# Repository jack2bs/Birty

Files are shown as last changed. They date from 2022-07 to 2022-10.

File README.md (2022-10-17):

# Birty the Robot

Birty is a recursive backronym for Birty Is a Robot, Thank You.

As part of my getting acquainted with robotics so as to continue in a leadership capacity in the Princeton Robotics Club, I set out to build a classic and simple, but well designed and well programmed robot which could drive in straight lines, turn accurate angles, avoid obstacles in it's path, and do it all autonomously. While these goals may not sound particularly ambitious or impressive, they are the baseline and the scaffolding for what a robot needs to be able to do.

I am proud of Birty. Birty is my most polished large project to date. The part-selection was, with one exception, well thought out. The electronics are well designed. The 3d structure of the Robot was well planned. The code is well written; it's fast, self-documenting (and documented with comments), and highly functional.

My success building Birty came on the back of the shortcomings of past projects, some of which never lived up to their potential simply due to my mistakes and inexperience. I learned from my mistakes, and I improved. I organized the project better. I worked with each sensor and electrical component before I used them to make sure they functioned as I expected them to. I tested each bit of code before moving onto another function. I took the time to do things right, and in the end it was the fastest I've ever completed a project. 

# Parts and justifications

+ Microcontroller
	+ 1 x [ATMEGA32u4](https://www.digikey.com/en/products/detail/microchip-technology/ATMEGA32U4-AUR/2238241)
	+ The Atmega32u4 is more than powerful enough for the tasks laid out, and since I had experience with it and had some in my supplies (every MCU was out of stock at the time), this was a no-brainer. An I2C bus (using the TWI peripheral) for sensor communications, USART for debugging over bluetooth, GPIO for driving motors, pin change interrupts for reading encoders, and more than enough timers for task scheduling.
+ Distance Sensors
	+ 8 x [Adafruit VL6180x](https://www.adafruit.com/product/3316)
	+ The VL6180x from STM was a good choice because it has great accuracy at low distance ranges which is extremely important for obstacle detection and avoidance for a robot of Birty's size. I chose the 6180x over other sensors in the lineup since it is the only one with a register map available, allowing me to bypass STM's poorly regarded API and simply build an I2C communication layer myself. I chose the Adafruit breakouts so that I wouldn't have to make them myself, and so that I had logic level shifting from 5v to 3.3v on both the interrupt and xshut signal lines.
+ Gyroscope
	+ 1 x [MinImu-9 v5](https://www.pololu.com/product/2738)
	+ This was perhaps the one mistake I made in part selection. The MiniImu-9 v5 from Polulu is a good IMU, but it doesn't have onboard fusion calculation and the speed of the Atmega32u4 makes a complex fusion calculation a challenge. In the future I would lean more towards something like a BNO055 from Bosch, which has on board fusion calculations and outputs roll pitch and yaw, as opposed to x, y, and z for a gyroscope, accelerometer, and magnetometer seperately.
+ Motors
	+ 2 x [Regular DC motors](https://www.adafruit.com/product/4639)
	+ 2 x [Stepper Motors](https://www.adafruit.com/product/4411)
	+ I have both stepper and DC motors and I am able to interchange them as I see fit. The choices here weren't too important but I wanted them as small as I could find, and so that is what I got. 
+ Motor mounts
	+ 1 x [DC Motor Mount](https://www.pololu.com/product/989)
	+ 2 x [Stepper Mount](https://www.pololu.com/product/3435)
+ DC Motor Driver (H Bridge)
	+ 4 x [H Bridges](https://www.adafruit.com/product/4489)
	+ I tested these H bridges on a breadboard before using them on Birty and they proved to be simple and effective.
+ Wheels
	+ 1 x (2 wheels) [Wheel pair](https://www.pololu.com/product/1424)
	+ I wanted somewhat large wheels to attempt to improve Birty's ability to handle semi-rough terrain (carpet).
+ Universal Mounting Hubs
	+ 1 x (2 hubs) [Mounting hub pair](https://www.pololu.com/product/1997)
+ Ball Casters
	+ 2 x [Ball casters](https://www.pololu.com/product/955)
	+ These were so that Birty wouldn't tilt forwards or backwards.
+ Spacers
	+ 1 x [2mm spacers](https://www.pololu.com/product/1980)
	+ 1 x [4mm spacers](https://www.pololu.com/product/1981)
	+ To space the ball casters to the right height.
+ Battery
	+ 1 x [CHAMP Portable Charger](https://www.gonimble.com/products/champ-portable-charger)
	+ I chose this battery pack because it was the smallest I could find and because I am a sucker for sustainability.
+ Battery Mounting
	+ 3 x [Battery Mounts](https://www.pololu.com/product/2677)
	+ I'll explain the battery mounting strategy further when I get to mechanical design.
+ Wire to Board conns
	+ 2 x [6 Pos Wire to Board](https://www.digikey.com/en/products/detail/on-shore-technology-inc/OSTVN06A150/1588866) and 1 x [2 Pos Wire to Board](https://www.digikey.com/en/products/detail/on-shore-technology-inc/OSTVN02A150/1588862)
+ Shift registers
	+  1 x [Shift Register](https://www.digikey.com/en/products/detail/texas-instruments/SN74HCS264DR/13562988)
	+ I'll get into the purpose of the shift register when I discuss the electronics.
+ Assorted SMD Resistors and Capacitors
	+ 3 x 5k R
	+ 2 x 10k R
	+ 1 x 100 R
	+ 2 x 22 R
	+ 6 x 0.1uF C
	+ 1 x 1uF C
	+ 2 x 22pF C
	+ Pushbuttons
	+ 16Mhz Crystal
	+ USB Receptacle
+ Header Pins
	+ 9 x [6 Pos Female Header pins](https://www.digikey.com/en/products/detail/sullins-connector-solutions/PPPC061LFBN-RC/810178)
	+ 1 x [5 Pos Female Header Pins](https://www.digikey.com/en/products/detail/sullins-connector-solutions/PPPC051LFBN-RC/810177)

# Electrical design
After choosing parts I set out to design the schematic and circuit boards. This process was relatively straight forward, except I had to find a way to use as few GPIO pins as possible. The first measure I took was introducing a shift register to access the xshut pins on the 8 VL6180x sensors. I needed to be able to shutdown the sensors one at a time so that I could change their I2C addresses away from their default of 0x29, and so a shift register allowed me to start them all shutdown, and then restart them and set their addresses one at a time. Next, I realized that each of the interrupt pins on the VL6180x sensors could be set as open drain, and thus I could attach them all to one GPIO pin and poll them to see which one triggered an interrupt. These two tricks saved me 6 and 7 GPIO pins each, such that by the end I had 4 extra GPIO pins not being used. The final schematic looked like this:
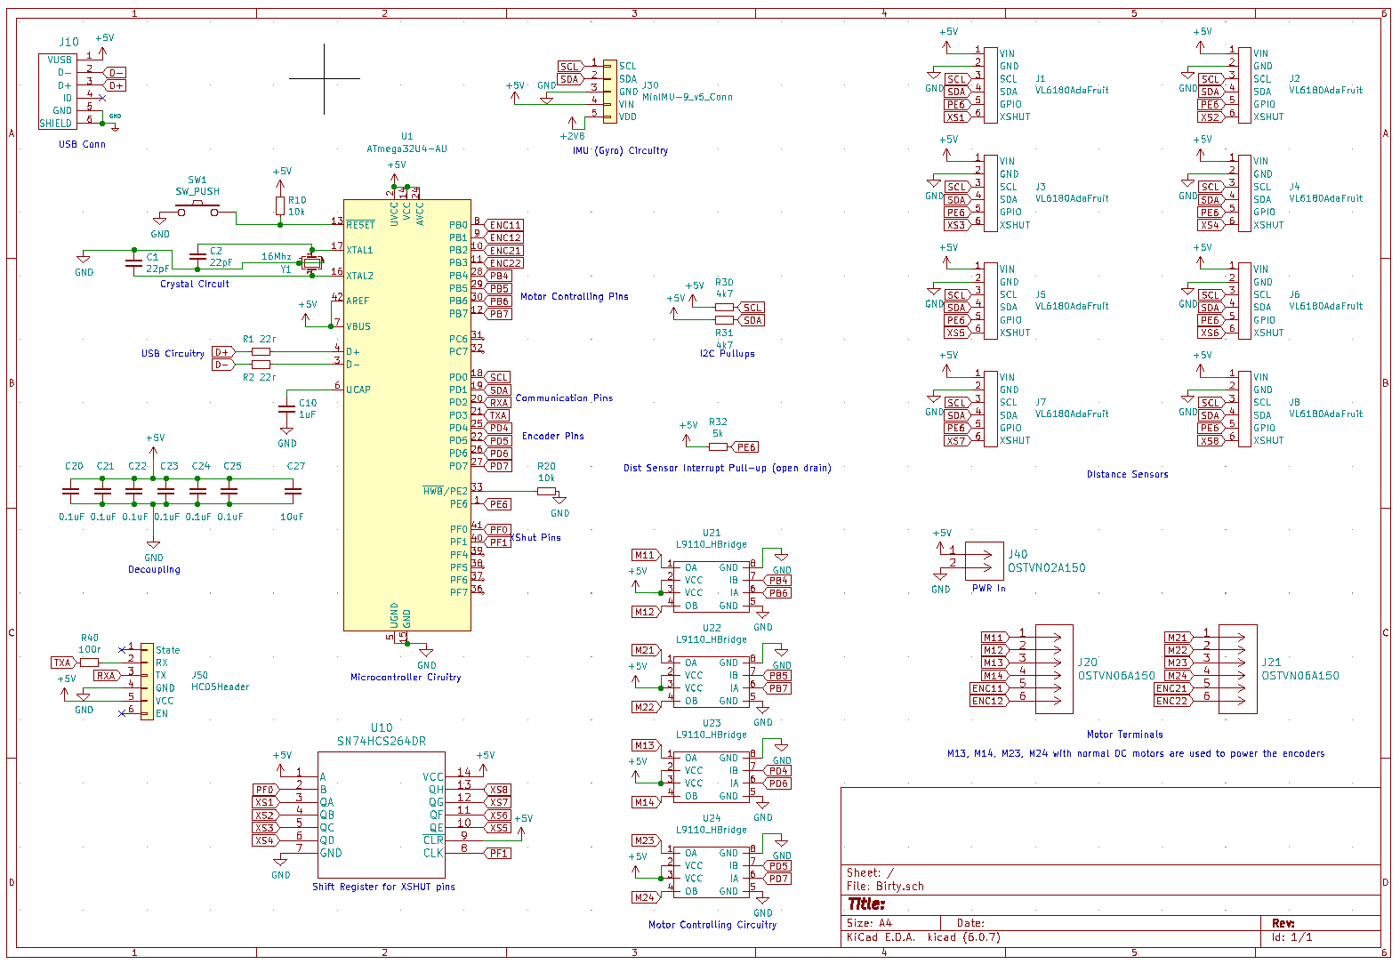
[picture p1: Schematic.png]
Schematic Image


I took this schematic and used it to produce a circuit board. I wanted every component on the top layer, which was not too difficult considering there was no real size constraint, and I wanted as large of a ground layer on the bottom layer of the board as possible, so I did the vast majority of my routing on the top layer as well. After a few hours of routing I had the following board.
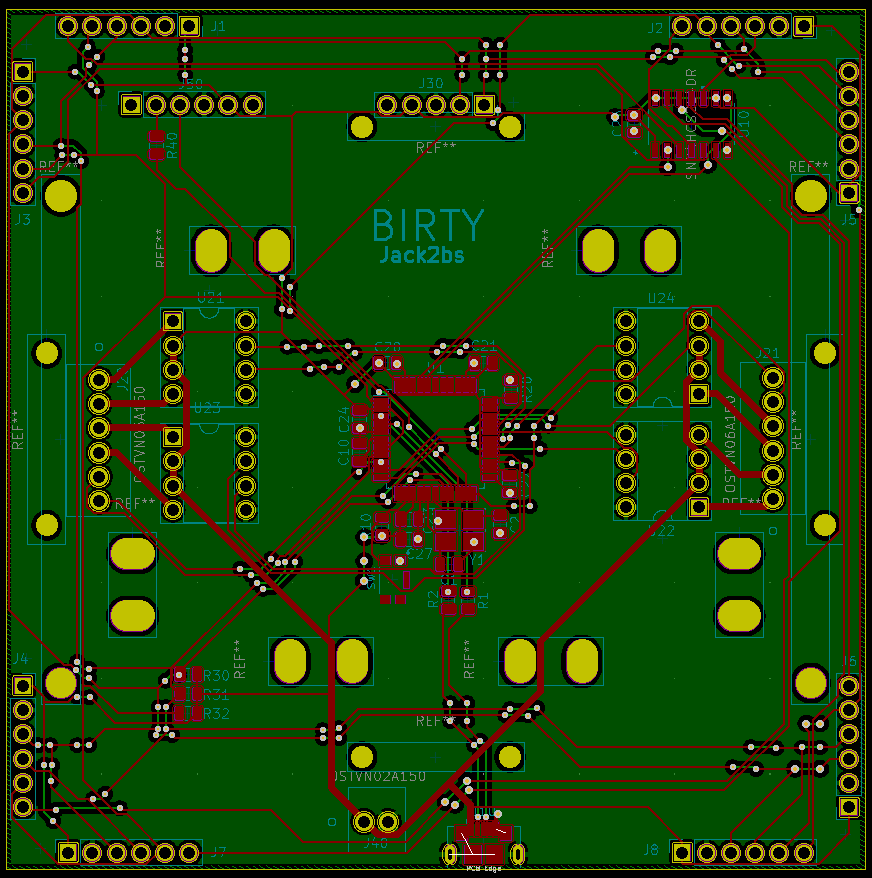
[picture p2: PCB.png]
PCB Image


# Mechanical Design
I knew that for a project that would exist in 3d space unlike any project I had done before, I would want to produce a 3d model of Birty so that I knew everything would fit together. It was during this process, I decided, that I would decide on how to mount the motors and battery pack to the robot. The motor mounts were as simple as adding mounting holes, but I knew the battery pack (which had no built in mounting method, seeing as it is just a portable phone charger) would be more difficult. After a significant amount of brainstorming, I decided upon a friction mount system based on stepper motor mounts which had a stiff hinge that allowed them to bend somewhere between -1 and 1 degree away from vertical. This allowed the battery pack to sit in between the mounts, as can be seen in the final picture of Birty at the very bottom of this README.

This was my first experience using Autocad Inventor, but I picked it up relatively quickly and the final product was the following 3d render.
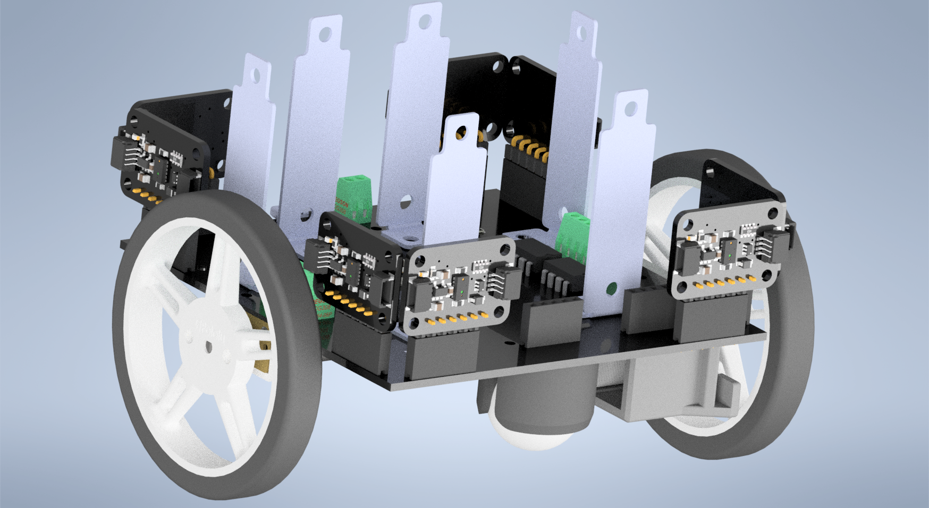
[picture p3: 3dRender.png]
3d render


# Programming
As could be expected for a project like this, writing the firmware took the most time. I started with a USART driver since I could use that for debugging, and then moved to an I2C driver so I could communicate with the sensors. Both the USART driver and I2C driver became bases for libraries I have since written. Next I moved onto code for receiving data from each of the sensors and then for communicating with the motors. Next I added some basic PID code for making sure the robot drove straight, and via testing determined that the Integral and Derivative components were not needed in Birty's case (the proportional control was enough). Finally I made sure that Birty could detect and avoid obstacles, or if near by a wall could drive straight and parallel to the wall.

# What went wrong and how did I fix it
Despite the relative success of building Birty, there were some hiccups-two short circuit incidents. The first short circuit occurred due to a lack of insulation between one of the motors and some of the H bridge's through hole pins. This ended up heating up the PCB to the point of destroying a small section of one of the encoder traces. I was fortunate that around a tenth of a millimeter of trace was exposed on either side, and so with a small piece of copper wire and some creative soldering I was able to bridge the damaged trace and cover it with electrical tape such that it has had no issues since. 

The second short circuit occurred when I plugged in the IMU wrong. Fortunately, only the IMU was damaged, and since I had ordered a spare, I was able to slot it in and continue as if nothing had happened. In addition, the IMU ended up being my least used sensor since I didn't want to give up clock cycles to a complicated fusion algorithm throughout my testing of Birty.

# Finally
Here are some pictures of Birty in my dorm room this year. Building Birty proved to me that when engineering is done right, it can be smooth and highly effective, which only reinforced just how beautiful this stuff can really be!

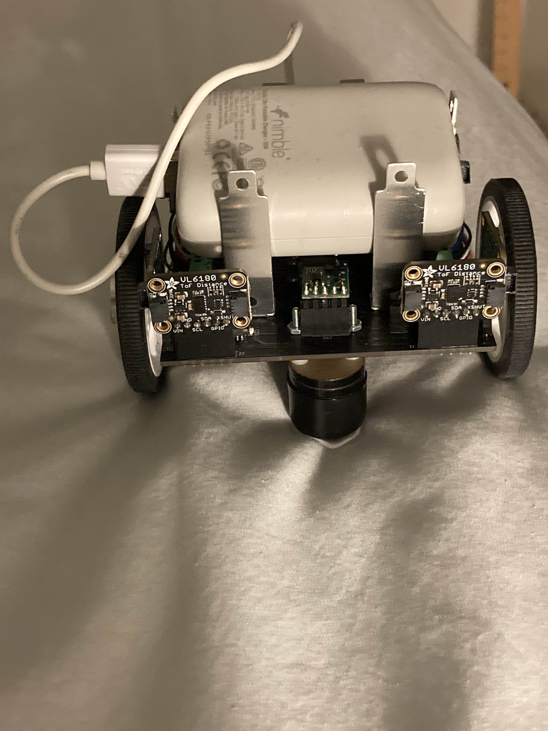
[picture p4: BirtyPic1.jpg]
Birty Picture 1

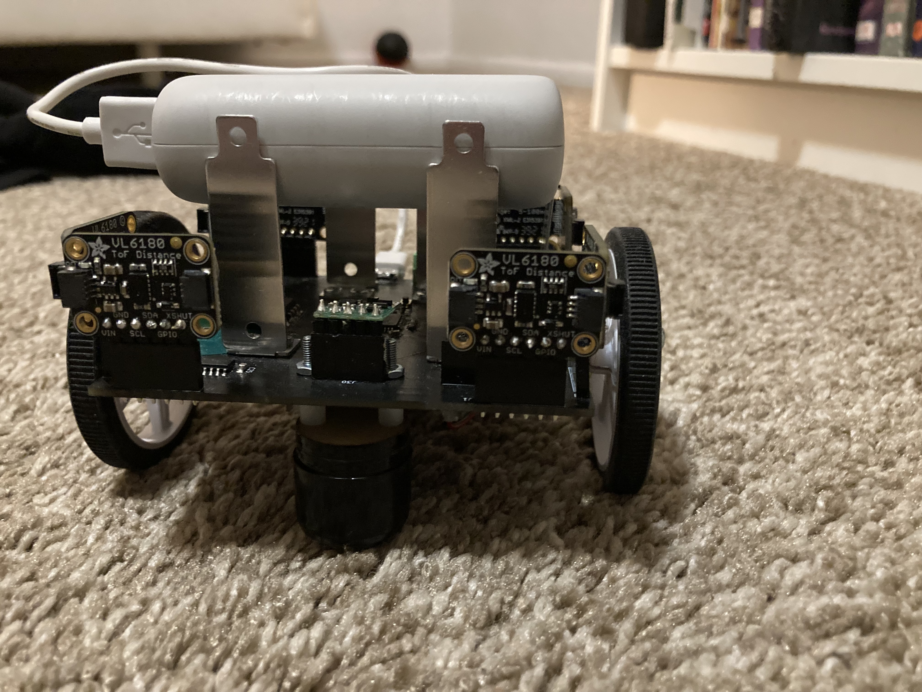
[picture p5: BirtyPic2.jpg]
Birty Picture 2


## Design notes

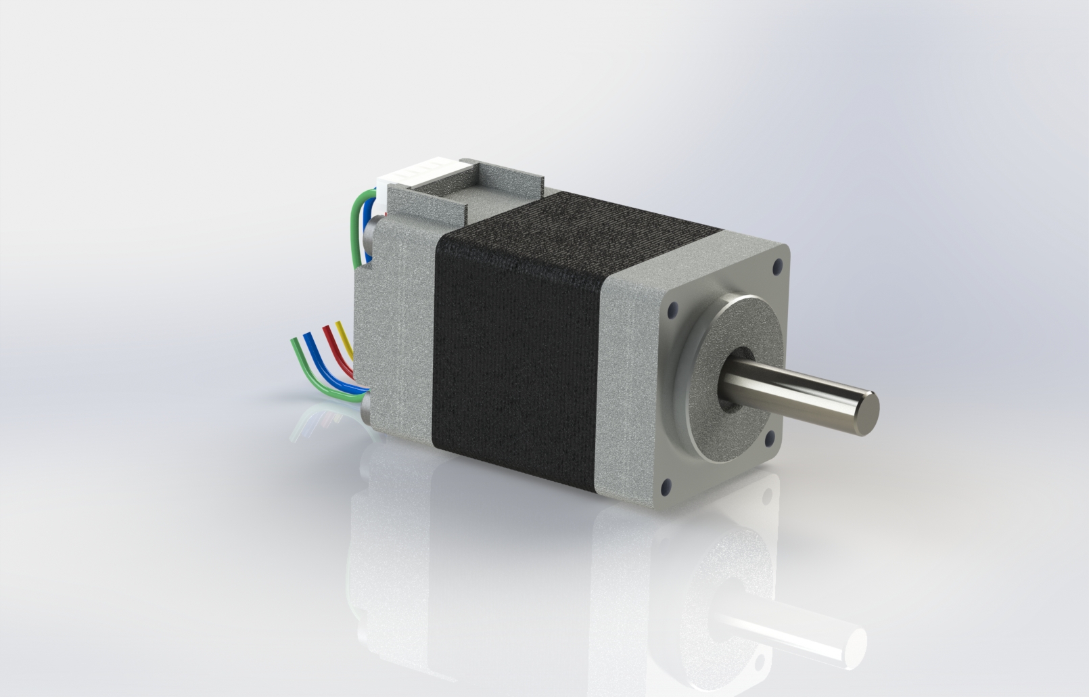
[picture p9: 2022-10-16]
3d Model/Birty/Motors/NEMA_8.JPG

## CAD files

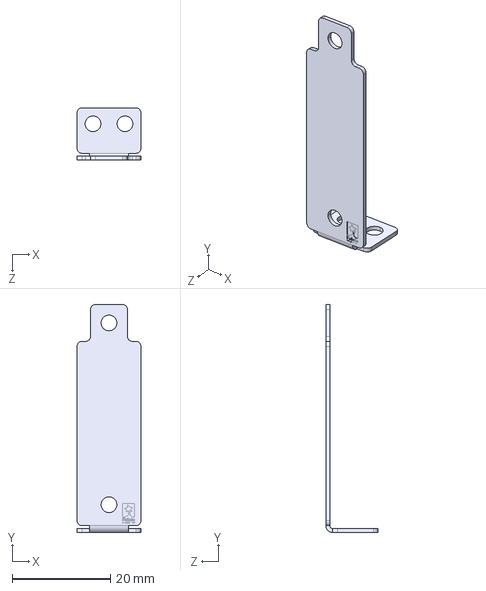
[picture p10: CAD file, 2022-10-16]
3d Model/Birty/Batteries/bracket-for-sharp-distance-sensors-perpendicular.step
13.0 x 46.4 x 10.7 mm

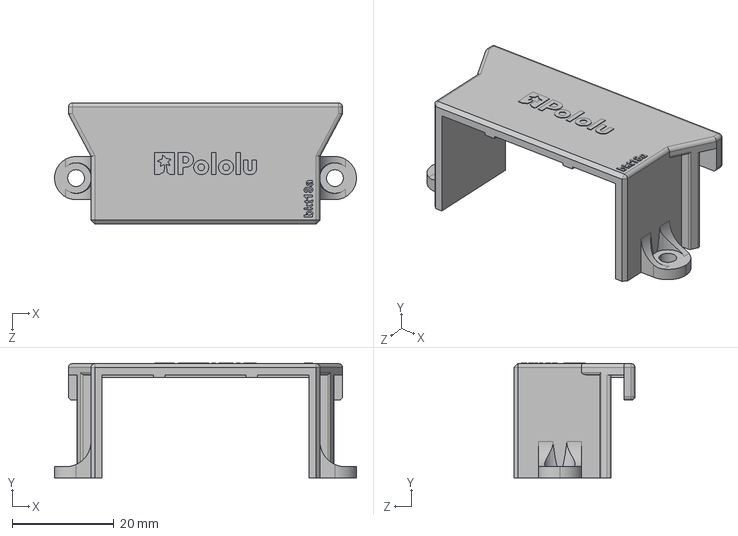
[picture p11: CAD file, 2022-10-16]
3d Model/Birty/Motor Holders/mounting-bracket-for-standard-size-servos.step
59.5 x 22.6 x 23.9 mm

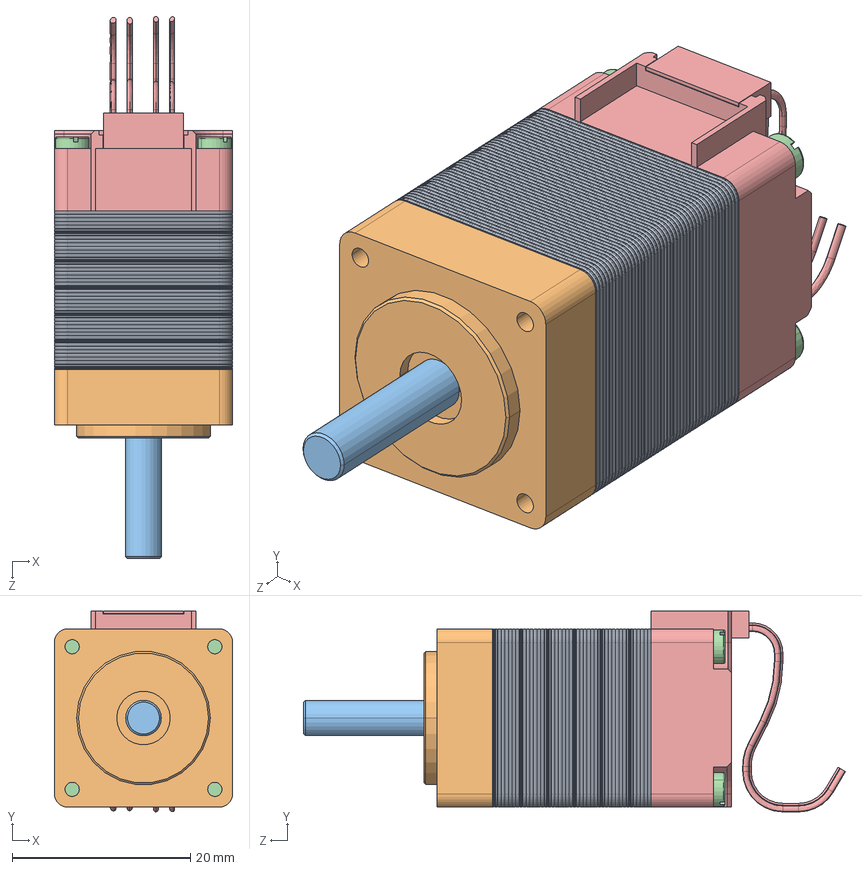
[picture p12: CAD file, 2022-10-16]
3d Model/Birty/Motors/NEMA8.STEP
20.0 x 22.5 x 60.8 mm
Stator
Lagerschild
Welle
Schraube_M2x28 x 4
Kollektorschild

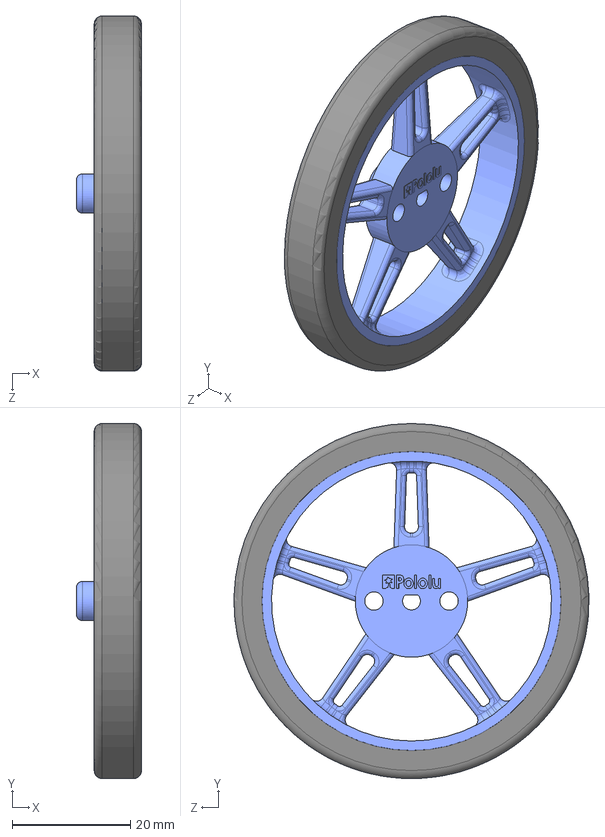
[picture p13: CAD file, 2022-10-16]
3d Model/Birty/Wheels/pololu-wheel-60x8mm-blue.step
11.0 x 60.0 x 60.0 mm

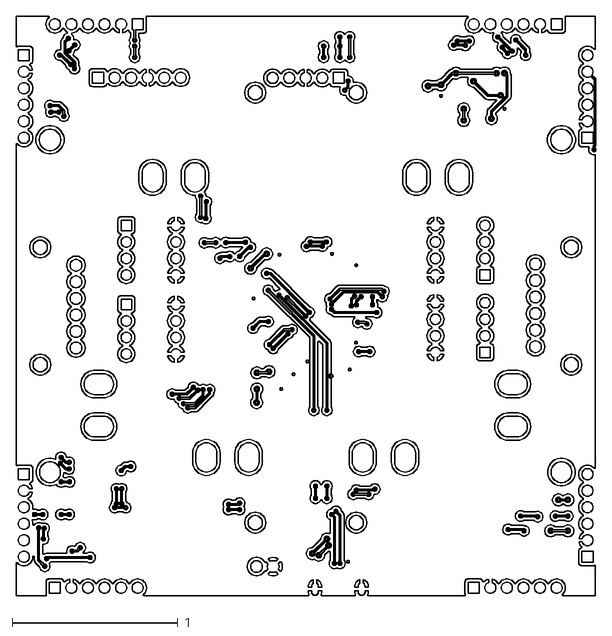
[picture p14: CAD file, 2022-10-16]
PCB and Schematic/Birty/Birty-B_Cu.dxf
3.50 x 3.50

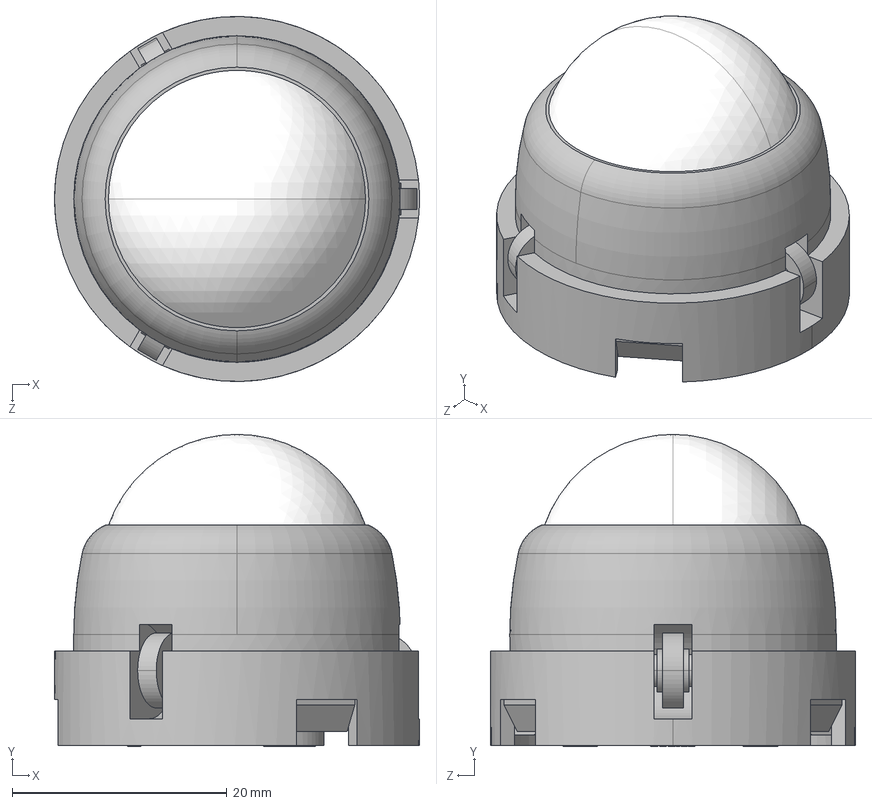
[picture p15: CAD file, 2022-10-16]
3d Model/Birty/Wheels/pololu-ball-caster-with-1in-plastic-ball-and-plastic-rollers.step
34.0 x 29.1 x 34.0 mm

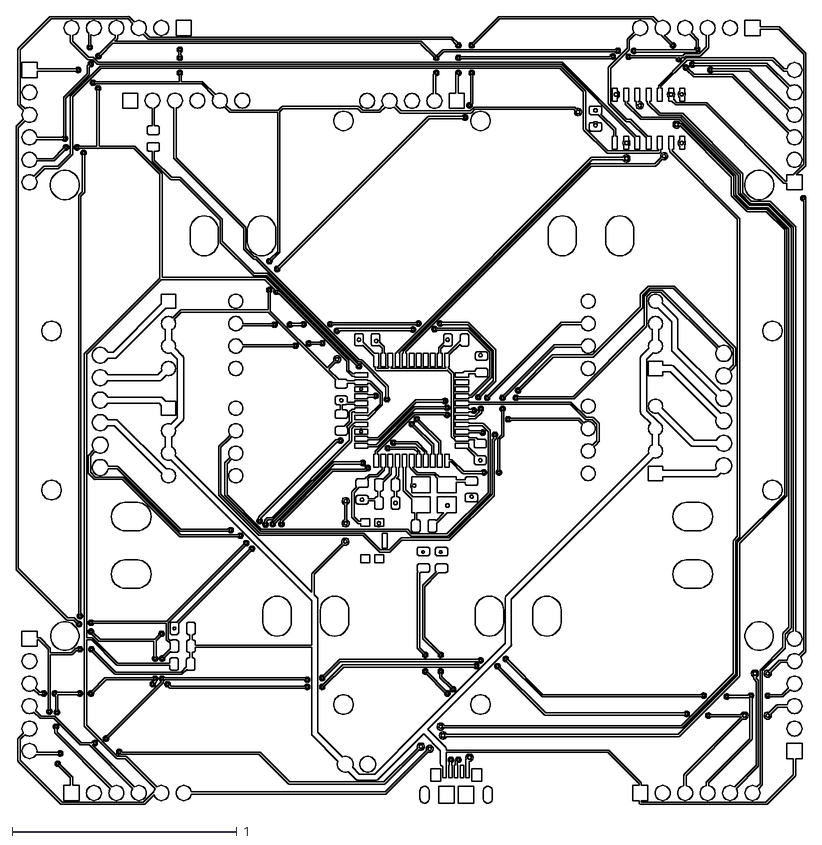
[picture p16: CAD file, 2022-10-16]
PCB and Schematic/Birty/Birty-F_Cu.dxf
3.52 x 3.51

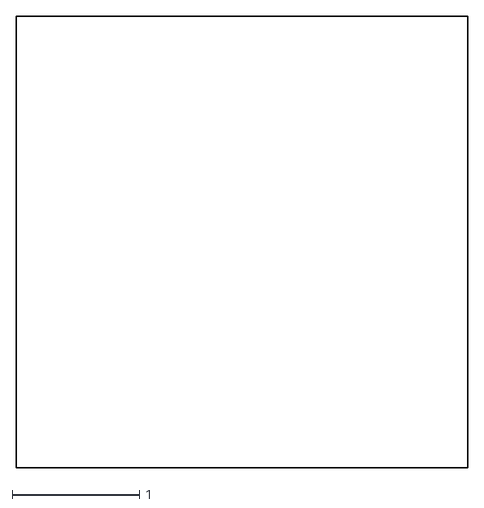
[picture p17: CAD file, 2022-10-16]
PCB and Schematic/Birty/Birty-Edge_Cuts.dxf
3.55 x 3.55

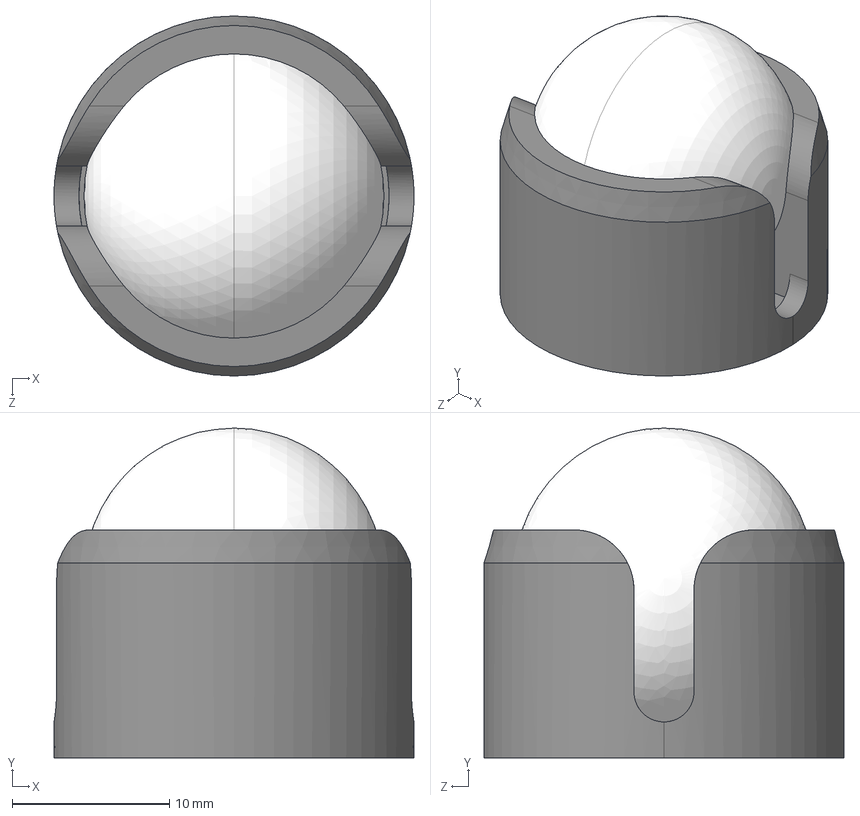
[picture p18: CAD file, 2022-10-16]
3d Model/Birty/Wheels/pololu-ball-caster-with-0-750in-metal-ball.step
22.9 x 20.9 x 22.9 mm

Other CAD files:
3d Model/Birty/Wheels/pololu-wheel-60x8mm-red.step
3d Model/Birty/Wheels/pololu-wheel-60x8mm-black.step
3d Model/Birty/Wheels/pololu-wheel-60x8mm-yellow.step
3d Model/Birty/Wheels/pololu-wheel-60x8mm-white.step
3d Model/Birty/Adafruit Dist Sensor/AdafruitDistSensor_Complete.iam
3d Model/Birty/Adafruit Dist Sensor/AdafruitDistSensor_NoHeaders.ipt
3d Model/Birty/Adafruit Dist Sensor/OldVersions/AdafruitDistSensor_Complete.0006.iam
3d Model/Birty/Adafruit Dist Sensor/Pin Header 1x6 TH Angle Pitch 2.54mm.ipt
3d Model/Birty/Batteries/CHAMP Portable.ipt
3d Model/Birty/Batteries/bracket-for-sharp-distance-sensors-perpendicular.ipt
3d Model/Birty/Birty.iam
3d Model/Birty/Main PCB/2ScrewTerm.ipt
3d Model/Birty/Main PCB/5FemaleHeader.ipt
3d Model/Birty/Main PCB/6FemaleHeader.ipt
3d Model/Birty/Main PCB/6ScrewTerm.ipt
3d Model/Birty/Main PCB/8PinDip.ipt
3d Model/Birty/Main PCB/Birty.iam
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

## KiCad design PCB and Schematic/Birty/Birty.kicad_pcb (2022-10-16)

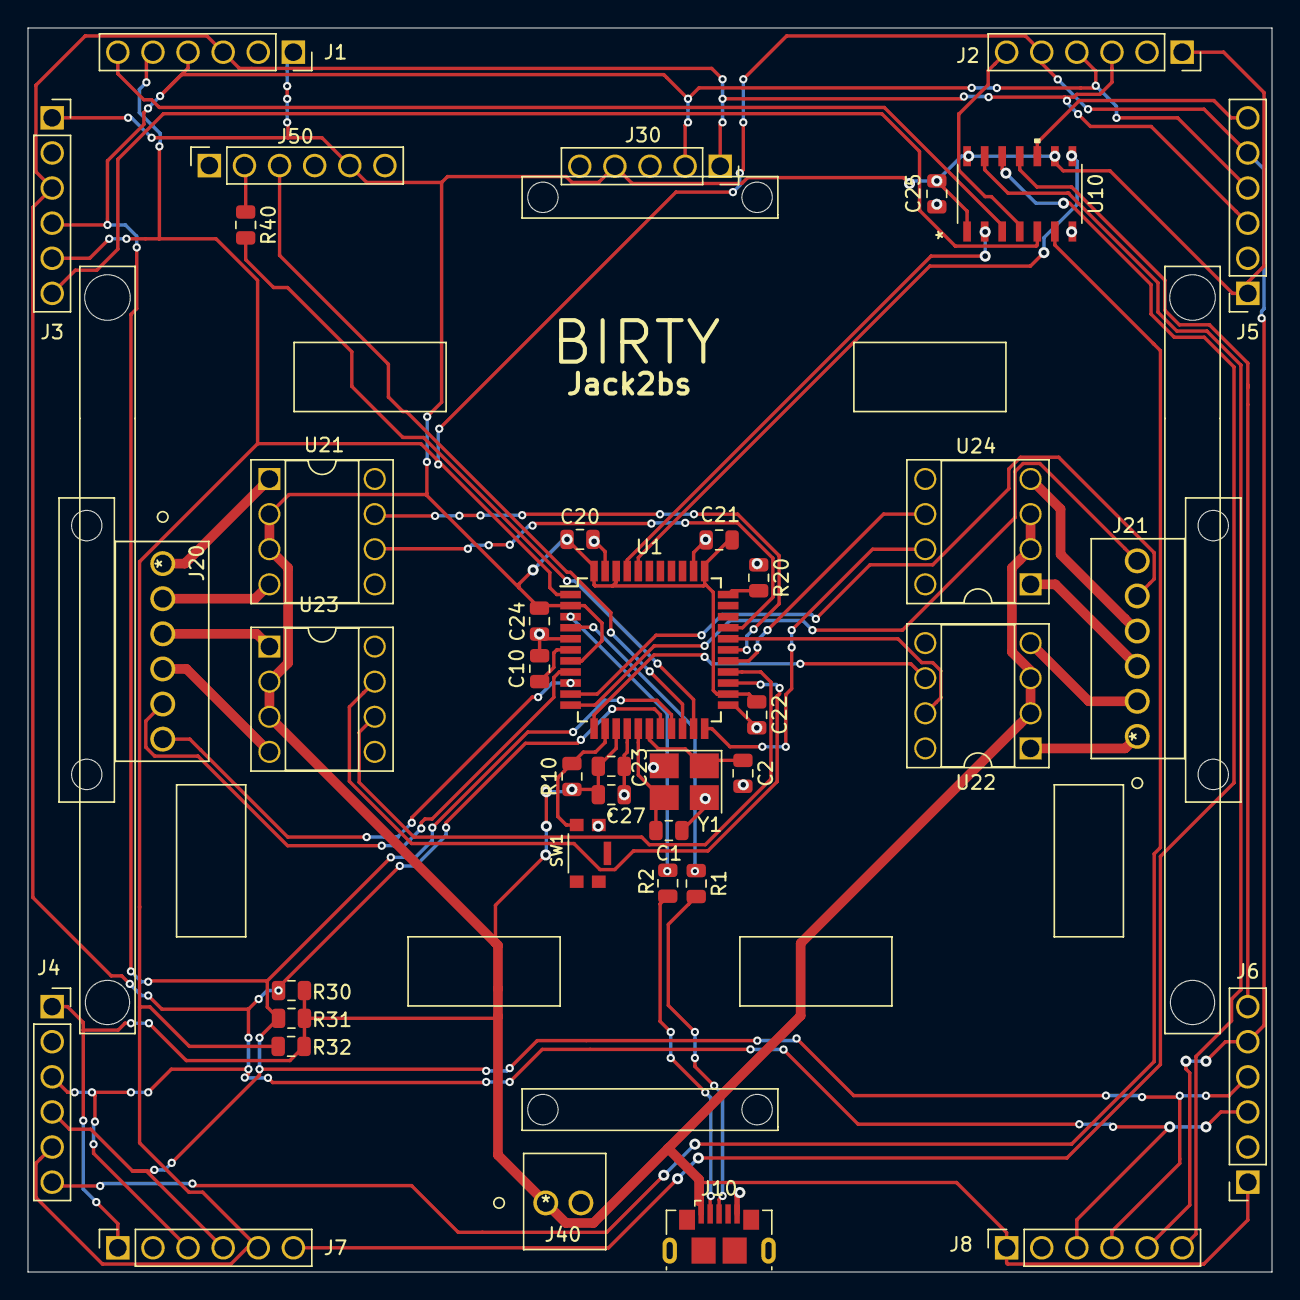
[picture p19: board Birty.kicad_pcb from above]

Board: 2 copper layers, 90.0 x 90.0 mm, 40 parts (0 on the bottom side), 47 nets.

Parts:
C1, C2: 22pF; C_0805_2012Metric
C10: 1uF; C_0805_2012Metric
C20, C21, C22, C23, C24, C25: 0.1uF; C_0805_2012Metric
C27: 10uF; C_0805_2012Metric
J1, J2, J3, J4, J5, J6, J7, J8: VL6180AdaFruit; VL6810AdaFruit
J10: USB_mini_micro_B; USB_Micro-B_GCT_USB3076-30-A
J20, J21: OSTVN06A150
J30: MinIMU-9_v5_Conn; MiniIMU-9-v5
J40: OSTVN02A150
J50: HC05Header
R1, R2: 22r; R_0805_2012Metric
R10, R20: 10k; R_0805_2012Metric
R30, R31: 4k7; R_0805_2012Metric
R32: 5k; R_0805_2012Metric
R40: 100r; R_0805_2012Metric
SW1: SW_PUSH; SW_KMR421GULCLFS
U1: ATmega32U4-AU; TQFP-44_10x10mm_P0.8mm
U10: SN74HCS264DR
U21, U22, U23, U24: L9110_HBridge; Adafruit_L9110_HBridge
Y1: 16Mhz; Crystal_SMD_3225-4Pin_3.2x2.5mm_HandSoldering

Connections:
+5V: C20.1, C21.1, C22.1, C23.1, C24.1, C25.1, C27.1, J1.1, J2.1, J3.1, J4.1, J5.1, J6.1, J7.1, J8.1, J10.1, J30.4, J40.1, J50.5, R10.1, R30.2, R31.1, R32.1, U1.2, U1.7, U1.14, U1.24, U1.34, U1.42, U1.44, U10.1, U10.9, U10.14, U21.2, U21.3, U22.2, U22.3, U23.2, U23.3, U24.2, U24.3
D+: J10.3, R1.2
D-: J10.2, R2.2
ENC11: J20.5, U1.8
ENC12: J20.6, U1.9
ENC21: J21.5, U1.10
ENC22: J21.6, U1.11
GND: C1.1, C2.2, C10.2, C20.2, C21.2, C22.2, C23.2, C24.2, C25.2, C27.2, J1.2, J2.2, J3.2, J4.2, J5.2, J6.2, J7.2, J8.2, J10.5, J10.6, J30.3, J40.2, J50.4, R20.1, SW1.1, U1.5, U1.15, U1.23, U1.35, U1.43, U10.7, U21.5, U21.8, U22.5, U22.8, U23.5, U23.8, U24.5, U24.8, Y1.2, Y1.4
M11: J20.1, U21.1
M12: J20.2, U21.4
M13: J20.3, U23.1
M14: J20.4, U23.4
M21: J21.1, U22.1
M22: J21.2, U22.4
M23: J21.3, U24.1
M24: J21.4, U24.4
unnamed: C1.2, U1.16, Y1.3
unnamed: C2.1, U1.17, Y1.1
unnamed: C10.1, U1.6
unnamed: J50.2, R40.1
unnamed: R1.1, U1.4
unnamed: R2.1, U1.3
unnamed: R10.2, SW1.2, U1.13
unnamed: R20.2, U1.33
PB4: U1.28, U21.7
PB5: U1.29, U22.7
PB6: U1.30, U21.6
PB7: U1.12, U22.6
PD4: U1.25, U23.7
PD5: U1.22, U24.7
PD6: U1.26, U23.6
PD7: U1.27, U24.6
PE6: J1.5, J2.5, J3.5, J4.5, J5.5, J6.5, J7.5, J8.5, R32.2, U1.1
PF0: U1.41, U10.2
PF1: U1.40, U10.8
RXA: J50.3, U1.20
SCL: J1.3, J2.3, J3.3, J4.3, J5.3, J6.3, J7.3, J8.3, J30.1, R30.1, U1.18
SDA: J1.4, J2.4, J3.4, J4.4, J5.4, J6.4, J7.4, J8.4, J30.2, R31.2, U1.19
TXA: R40.2, U1.21
XS1: J1.6, U10.3
XS2: J2.6, U10.4
XS3: J3.6, U10.5
XS4: J4.6, U10.6
XS5: J5.6, U10.10
XS6: J6.6, U10.11
XS7: J7.6, U10.12
XS8: J8.6, U10.13

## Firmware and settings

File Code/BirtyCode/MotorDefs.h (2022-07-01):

/*
 * MotorDefs.h
 *
 * Created: 5/29/2022 9:06:52 PM
 *  Author: Jack2bs
 */ 


#ifndef MOTORDEFS_H_
#define MOTORDEFS_H_

// Motor Direction Defines
#define DIR_BACKWARD	0
#define DIR_FORWARD		1

/* Motor right left defines. USE THESE*/

// Defines for passing motor sides as arguments
#define RIGHT_MOTOR_PASS		0b01
#define LEFT_MOTOR_PASS			0b10
#define BOTH_MOTORS_PASS		0b11

// Defines for choosing motor in arrays
#define RIGHT_MOTOR_INDEX		(RIGHT_MOTOR_PASS - 1)
#define LEFT_MOTOR_INDEX		(LEFT_MOTOR_PASS - 1)

#endif /* MOTORDEFS_H_ */

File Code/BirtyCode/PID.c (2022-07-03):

/*
 * PID.c
 *
 * Created: 6/20/2022 8:11:45 PM
 *  Author: Jack2bs
 */ 

#include "Encoder.h"
#include "DCMotor.h"
#include "PID.h"
#include "MotorDefs.h"
#include "VL6180XDist.h"


static int g_motionState = NO_MOTION_STATE;
static const long g_distForTurnInMinus7PerDegree =  19548;

static long g_distThresh = 0;

int getMotionState()
{
	return g_motionState;
}

void stopMoving()
{
	g_motionState = NO_MOTION_STATE;
	setMotorPWR(BOTH_MOTORS_PASS, 0);
	g_distThresh = 0;
}

void startMovingBackwards()
{
	resetDists();
	
	g_motionState = MOVING_BACKWARDS_STATE;
	setMotorDir(BOTH_MOTORS_PASS, DIR_BACKWARD);
	setMotorPWR(BOTH_MOTORS_PASS, 80);
}

void startMovingStraight()
{
	resetDists();
	
	g_motionState = MOVING_STRAIGHT_STATE;
	setMotorDir(BOTH_MOTORS_PASS, DIR_FORWARD);
	setMotorPWR(BOTH_MOTORS_PASS, 80);
}

void startLeftTurn()
{
	
	g_motionState = TURNING_LEFT_STATE;
	
	resetDists();
	
	setMotorDir(LEFT_MOTOR_PASS, DIR_FORWARD);
	
	setRightMotorPWR(80);
	setLeftMotorPWR(0);
}

void startRightTurn()
{
	g_motionState = TURNING_RIGHT_STATE;
	
	resetDists();
	
	setMotorDir(RIGHT_MOTOR_PASS, DIR_FORWARD);
	
	setLeftMotorPWR(80);
	setRightMotorPWR(0);
}

void turnRight(uint16_t degrees)
{
	g_distThresh = g_distForTurnInMinus7PerDegree * degrees;
	startRightTurn();
}
void turnLeft(uint16_t degrees)
{
	g_distThresh = g_distForTurnInMinus7PerDegree * degrees;
	startLeftTurn();
}

void moveStraight(long distCM)
{
	g_distThresh = distCM * 100000;
	
	startMovingStraight();
}

void moveBackwards(long distCM)
{
	g_distThresh = distCM * -100000;
	
	startMovingBackwards();
}

void updateMotionState()
{
	switch (g_motionState)
	{
	case MOVING_STRAIGHT_STATE:
		if (((getRightDistAccurate() + getLeftDistAccurate()) / 2) > g_distThresh)
		{
			stopMoving();
		}
		break;
	case TURNING_LEFT_STATE:
		if ((getRightDistAccurate() - getLeftDistAccurate()) > g_distThresh)
		{
			stopMoving();
		}
		break;
	case TURNING_RIGHT_STATE:
		if ((getLeftDistAccurate() - getRightDistAccurate()) > g_distThresh)
		{
			stopMoving();
		}
		break;
	case MOVING_BACKWARDS_STATE:
		if (((getRightDistAccurate() + getLeftDistAccurate()) / 2) < g_distThresh)
		{
			stopMoving();
		}
		break;
	}
}


void equalizeSpeedsStraight()
{
	static const long equalization_factor = 50000;
	long diff = getLeftDistAccurate() - getRightDistAccurate();
	long refactoredDiff = diff / equalization_factor;
	int rmp = 80;
	int lmp = 80;
	if (g_motionState == MOVING_STRAIGHT_STATE)
	{
		rmp += refactoredDiff;
		lmp -= refactoredDiff;
	}
	if (g_motionState == MOVING_BACKWARDS_STATE)
	{
		rmp -= refactoredDiff;
		lmp += refactoredDiff;
	}
	
	if (rmp > 100)
	{
		setRightMotorPWR(100);
	}
	else if (rmp < 0)
	{
		setRightMotorPWR(0);
	}
	else
	{
		setRightMotorPWR(rmp);
	}
	
	if (lmp > 100)
	{
		setLeftMotorPWR(100);
	}
	else if (lmp < 0)
	{
		setLeftMotorPWR(0);
	}
	else
	{
		setLeftMotorPWR(lmp);
	}
}

void avoidWallsBackward()
{
	static const long equalizationFacor = 1;
	
	int ba_r = getDistSensorDist(BACK_RIGHT_INDEX);
	int ba_l = getDistSensorDist(BACK_LEFT_INDEX);
	
	if (ba_r < 40 || ba_l < 40)
	{
		stopMoving();
		return;
	}
	
	int r_fr = getDistSensorDist(RIGHT_FRONT_INDEX);
	int r_ba = getDistSensorDist(RIGHT_BACK_INDEX);
	int l_fr = getDistSensorDist(LEFT_FRONT_INDEX);
	int l_ba = getDistSensorDist(LEFT_BACK_INDEX);
	
	if (r_ba < 65)
	{
		int diff = (r_fr - r_ba) / equalizationFacor;
		setRightMotorPWR(80 - diff);
		setLeftMotorPWR(80 + diff);
	}
	else if (l_ba < 65)
	{
		int diff = (l_fr - l_ba) / equalizationFacor;
		setRightMotorPWR(80 + diff);
		setLeftMotorPWR(80 - diff);
	}
	else
	{
		equalizeSpeedsStraight();
	}
	
}

void avoidWallsForward()
{
	static const long equalizationFacor = 1;
	
	int fr_r = getDistSensorDist(FRONT_RIGHT_INDEX);
	int fr_l = getDistSensorDist(FRONT_LEFT_INDEX);
	
	if (fr_r < 55 || fr_l < 55)
	{
		stopMoving();
		return;
	}
	
	int r_fr = getDistSensorDist(RIGHT_FRONT_INDEX);
	int r_ba = getDistSensorDist(RIGHT_BACK_INDEX);
	int l_fr = getDistSensorDist(LEFT_FRONT_INDEX);
	int l_ba = getDistSensorDist(LEFT_BACK_INDEX);
	
	if (r_fr < 65)
	{
		int diff = (r_ba - r_fr) / equalizationFacor;
		setRightMotorPWR(80 + diff);
		setLeftMotorPWR(80 - diff);
	}
	else if (l_fr < 65)
	{
		int diff = (l_ba - l_fr) / equalizationFacor;
		setRightMotorPWR(80 - diff);
		setLeftMotorPWR(80 + diff);
	}
	else
	{
		equalizeSpeedsStraight();
	}
	
}

void updateMotors()
{
	switch (g_motionState)
	{
	case NO_MOTION_STATE:
		break;
	case MOVING_STRAIGHT_STATE:
		avoidWallsForward();
		break;
	case MOVING_BACKWARDS_STATE:
		avoidWallsBackward();
		break;
	default:
		break;
	}
}

void motionTask()
{
	if (g_motionState != NO_MOTION_STATE)
	{
		updateMotionState();
	}
	updateMotors();
}

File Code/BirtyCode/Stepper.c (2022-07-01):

/*
 * Stepper.c
 *
 * Created: 5/29/2022 11:10:15 AM
 *  Author: Jack2bs
 */ 

// Other includes
#include <stdint.h>
#include <avr/io.h>
#include <avr/interrupt.h>

// Custom includes
#include "Stepper.h"
#include "MotorDefs.h"

// This variable stores the 1% power TOP for the stepper CTC
static const int minPower = 18800;

// This stores the direction of the two stepper motors
static uint8_t g_direction[2] = {DIR_FORWARD, DIR_FORWARD};

// This occurs at TOP for the left motor's CTC
ISR(TIMER1_COMPA_vect)
{
	fullStepLeft(g_direction[LEFT_MOTOR_INDEX]);
}

// This occurs at TOP for the right motor's CTC
ISR(TIMER3_COMPA_vect)
{
	fullStepRight(g_direction[RIGHT_MOTOR_INDEX]);
}



// This sets the left stepper's direction
void setStepperMotorDirLeft(uint8_t dir)
{
	g_direction[LEFT_MOTOR_INDEX] = dir;
}

// This sets the right stepper's direction
void setStepperMotorDirRight(uint8_t dir)
{
	g_direction[RIGHT_MOTOR_INDEX] = dir;
}

// This sets either or both motor's direction
void setStepperMotorDir(uint8_t rightOrLeft, uint8_t dir)
{
	if (rightOrLeft & RIGHT_MOTOR_PASS)
	{
		g_direction[RIGHT_MOTOR_INDEX] = dir;
	}
	if (rightOrLeft & LEFT_MOTOR_PASS)
	{
		g_direction[LEFT_MOTOR_INDEX] = dir;
	}
}



// This returns the direction of the Left motor
uint8_t getStepperMotorDirLeft()
{
	return g_direction[LEFT_MOTOR_INDEX];
}

// This returns the direction of the Right motor
uint8_t getStepperMotorDirRight()
{
	return g_direction[RIGHT_MOTOR_INDEX];
}

// This returns the direction of either stepper
uint8_t getStepperMotorDir(uint8_t rightOrLeft)
{
	return g_direction[rightOrLeft - 1];
}



// This returns the power of the left stepper as a percentage
int getStepperPowerLeft()
{
	int temp = OCR1A;
	return (minPower / temp);
}

// This returns the power of the right stepper as a percentage
int getStepperPowerRight()
{
	int temp = OCR3A;
	return (minPower / temp);
}

// This returns the power of one of the motors
int getStepperPower(int rightOrLeft)
{
	// If the Right motor was selected
	if (rightOrLeft == RIGHT_MOTOR_PASS)
	{
		return getStepperPowerRight();
	}
	// Else if the left motor was selected
	else if (rightOrLeft == LEFT_MOTOR_PASS)
	{
		return getStepperPowerLeft();
	}
	// Else return -1
	return -1;
}



// The sets the left stepper motor's power
void setStepperPowerLeft(int percent)
{
	// If it's 0 percent
	if (!percent)
	{
		// Disable the CTC
		TCCR1B = 0x00;
		return;
	}
	
	// Reinitialize the left stepper motor's timer (in case we are recovering from 0%)
	stepperTimerLeftInit();
	
	// Divide the minimum power by the percent to get our TOP value
	OCR1A = (uint16_t)(minPower / percent);
}

// The sets the right stepper motor's power
void setStepperPowerRight(int percent)
{
	// If it's 0 percent
	if (!percent)
	{
		// Disable the CTC
		TCCR3B = 0x00;
		return;
	}
	
	// Reinitialize the left stepper motor's timer (in case we are recovering from 0%)
	stepperTimerRightInit();
	
	// Divide the minimum power by the percent to get our TOP value
	OCR3A = (uint16_t)(minPower / percent);
}

// This sets either or both stepper's power
void setStepperPower(int rightOrLeft, int percent)
{
	// If Left or Both is passed
	if (rightOrLeft & LEFT_MOTOR_PASS)
	{
		setStepperPowerLeft(percent);		// Set the left motor's power
	}
	// If Right or Both is passed
	if (rightOrLeft & RIGHT_MOTOR_PASS)
	{
		setStepperPowerRight(percent);		// Set the right motor's power
	}
}



// Have the left motor take a full step
void fullStepLeft(uint8_t forwardBackward)
{
	// This stores the next state of the Left stepper
	static int8_t l_state = 0;
	
	/*
	States:
	0: B4, D4
	1: B6, D4
	2: B6, D6
	3: B4, D6
	*/
	
	// Switch: the state of the left stepper
	switch (l_state)
	{
	// Move the motor to l_state
	case 0:
		PORTD |= (1<<PORTD4);
		PORTB |= (1<<PORTB4);
		PORTD &= ~(1<<PORTD6);
		PORTB &= ~(1<<PORTB6);
		break;
	case 1:
		PORTD |= (1<<PORTD4);
		PORTB |= (1<<PORTB6);
		PORTD &= ~(1<<PORTD6);
		PORTB &= ~(1<<PORTB4);
		break;
	case 2:
		PORTD |= (1<<PORTD6);
		PORTB |= (1<<PORTB6);
		PORTD &= ~(1<<PORTD4);
		PORTB &= ~(1<<PORTB4);
		break;
	case 3:
		PORTD |= (1<<PORTD6);
		PORTB |= (1<<PORTB4);
		PORTD &= ~(1<<PORTD4);
		PORTB &= ~(1<<PORTB6);
		break;
	default:
		l_state = 0;	
		return;
	}
	
	// If the motor is supposed to be moving forward
	if (forwardBackward == DIR_FORWARD)
	{
		l_state++;	// Increment the l_state
	}
	// Otherwise
	else
	{
		l_state--;	// Decrement the l_state
	}
	
	// If the motor's state was incremented too high
	if (l_state > 3)
	{
		// Reset it to 0
		l_state = 0;
	}
	// Otherwise if it is decremented too low
	else if (l_state < 0)
	{
		// Reset it to 3
		l_state = 3;
	}
}

// Have the right motor take a full step
void fullStepRight(uint8_t forwardBackward)
{
	// This stores the next state of the Right stepper
	static int8_t r_state = 0;
	
	/*
	States:
	0: B5, D5
	1: B7, D5
	2: B7, D7
	3: B5, D7
	*/
	
	// Switch: the state of the right stepper
	switch (r_state)
	{
	// Move the motor to r_state
	case 0:
		PORTD |= (1<<PORTD5);
		PORTB |= (1<<PORTB5);
		PORTD &= ~(1<<PORTD7);
		PORTB &= ~(1<<PORTB7);
		break;
	case 1:
		PORTD |= (1<<PORTD5);
		PORTB |= (1<<PORTB7);
		PORTD &= ~(1<<PORTD7);
		PORTB &= ~(1<<PORTB5);
		break;	
	case 2:
		PORTD |= (1<<PORTD7);
		PORTB |= (1<<PORTB7);
		PORTD &= ~(1<<PORTD5);
		PORTB &= ~(1<<PORTB5);
		break;
	case 3:
		PORTD |= (1<<PORTD7);
		PORTB |= (1<<PORTB5);
		PORTD &= ~(1<<PORTD5);
		PORTB &= ~(1<<PORTB7);
		break;
	default:
		r_state = 0;	
		return;
	}
	
	// If the motor is supposed to be moving forward
	if (forwardBackward == DIR_FORWARD)
	{
		r_state++;	// Increment the r_state
	}
	// Otherwise
	else
	{
		r_state--;	// Decrement the r_state
	}
	
	// If the motor's state was incremented too high
	if (r_state > 3)
	{
		// Reset it to 0
		r_state = 0;
	}
	// Otherwise if it is decremented too low
	else if (r_state < 0)
	{
		// Reset it to 3
		r_state = 3;
	}
}



// Initialize the timer of the left stepper motor
inline void stepperTimerLeftInit()
{
	// Set the timer to CTC mode only interrupting at TOP
	TCCR1B |= (1<<WGM12) | (1<<CS10) | (1<<CS11);
	TIMSK1 |= (1<<OCIE1A);
}

// Initialize the timer of the right stepper motor
inline void stepperTimerRightInit()
{
	// Set the timer to CTC mode only interrupting at TOP
	TCCR3B |= (1<<WGM32) | (1<<CS30) | (1<<CS31);
	TIMSK3 |= (1<<OCIE3A);
}

// Initialize both motor's timers
void stepperTimerInit()
{
	stepperTimerLeftInit();
	stepperTimerRightInit();
}



// Initialize the stepper motors
void stepperInit()
{
	// Set all stepper motor controlling pins to outputs
	DDRB |= (1<<DDB4) | (1<<DDB5) | (1<<DDB6) | (1<<DDB7);
	DDRD |= (1<<DDD4) | (1<<DDD5) | (1<<DDD6) | (1<<DDD7);
	
	// Initialize the stepper timers
	stepperTimerInit();
	
	// This could be removed
	setStepperPower(BOTH_MOTORS_PASS, 0);
}

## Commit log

2022-09-16 Remove inline just in case
2022-10-16 Added some photos
    [2ScrewTerm.ipt, 5FemaleHeader.0001.ipt, 5FemaleHeader.ipt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]

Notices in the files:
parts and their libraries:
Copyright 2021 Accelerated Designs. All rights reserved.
